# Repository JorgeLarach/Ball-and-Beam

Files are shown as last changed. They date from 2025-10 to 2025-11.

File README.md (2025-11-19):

# Ball and Beam System
Jorge Larach
_11/18/25_

This is my repository for my ball and beam system. Here you will find firmware for an STM32 Nucleo that allows it to interface with a distance sensor and a servo to control the position of a ball along the surface of a beam.

You will also find in the "Notes" directory plots that I used to measure PID performance, written in Python using Matplotlib, part drawings from Fusion, as well as more pictures. 

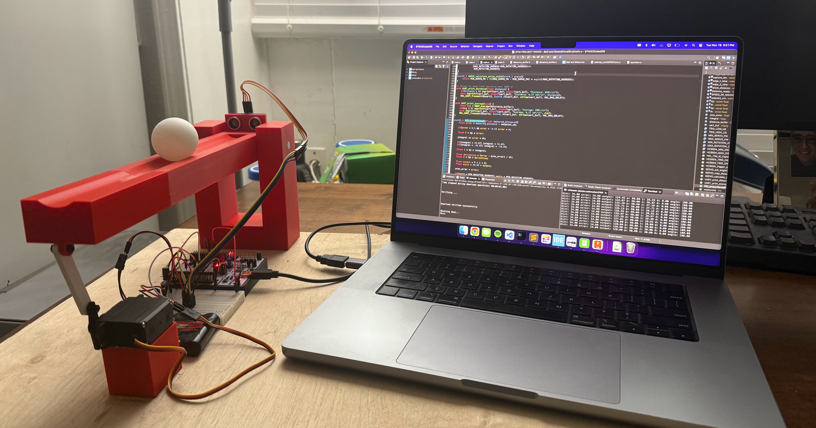
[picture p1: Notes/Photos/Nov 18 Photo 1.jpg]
PID Ball and Beam Project


Below are all of the parts that I used making this project:
* STM32 Nucleo-F401RE
* HC-SR04 Ultrasonic distance sensor
* MG996R Servo
* 6V 2000 mAh NiMH battery
* Small Breadboard
* 3D printed structure (tower, beam, etc.)
* M3 nuts, bolts, and washers
* 1 ping pong ball

Here's a few test results plotted out in Matplotlib. Below is what my first (working) attempt looked like
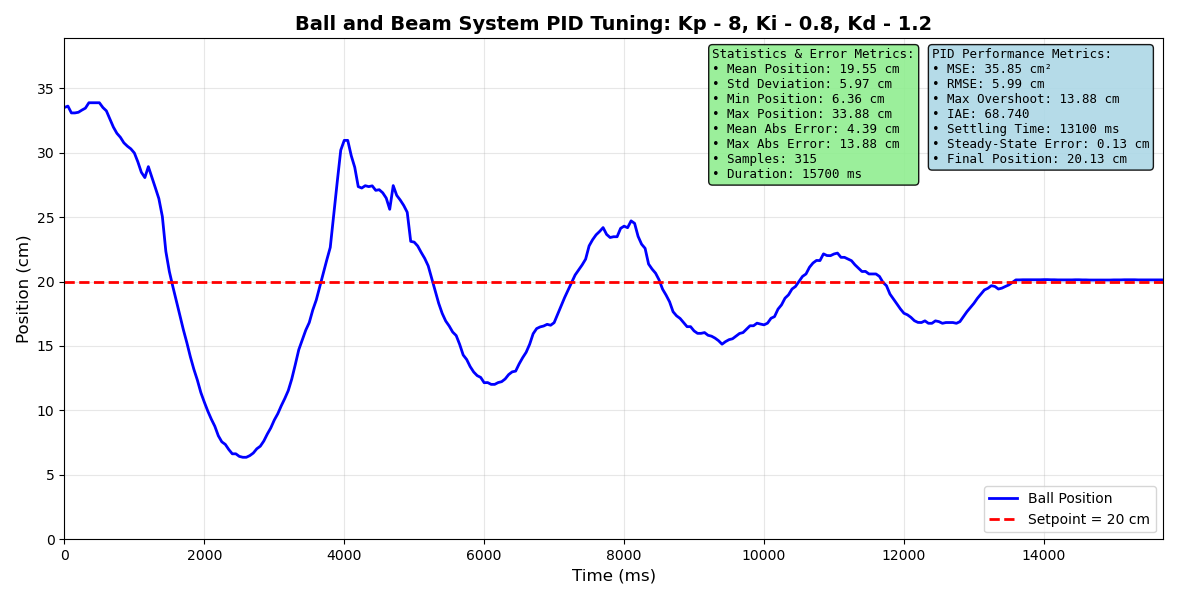
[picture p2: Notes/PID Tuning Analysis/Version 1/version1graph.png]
Version 1


Below is the version currently used by the algorithm. It is definitely far from perfect, but it is a major improvement over the first version (nearly halved the MSE!) There's far less oscillations, but it looks like there's potentially some steady-state error, where the ball approaches the setpoint early on, but seems to hover underneath it for a while.
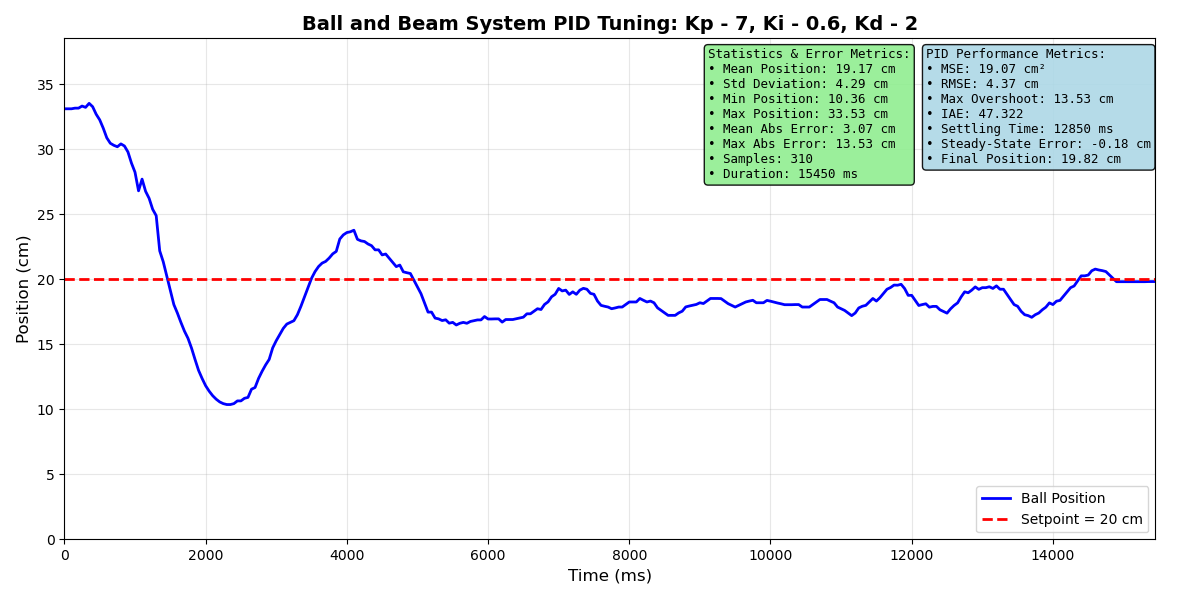
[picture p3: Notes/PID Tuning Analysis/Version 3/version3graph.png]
Version 3


I carved the groove in the beam from a 4 cm diameter circle in Fusion, so it perfectly fits any ping pong ball. My Bambulabs A1 printer couldn't print a beam longer than 25.6 cm due to the print bed size, so I designed it in two steps, consisting of a long bridge part and a short bridge part (during development I decided it would be called a "bridge" instead of "beam"; I don't know exactly what posessed me to do that) using two cylindrical pegs. Below is the Fusion drawing for the long bridge part:
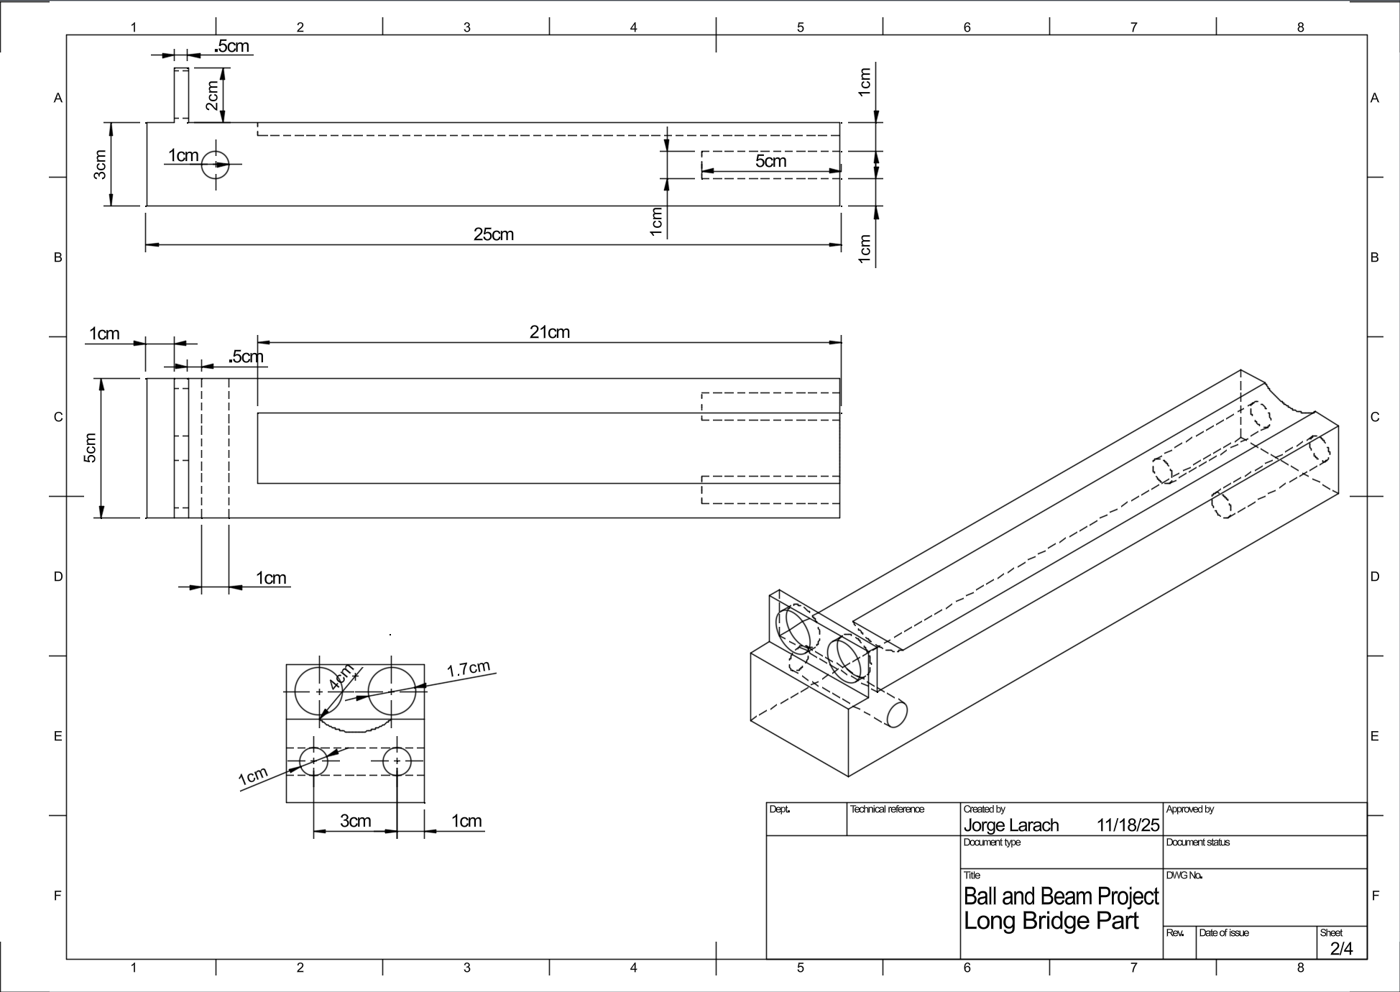
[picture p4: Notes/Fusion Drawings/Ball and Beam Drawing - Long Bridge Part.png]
Fusion drawing for long bridge part


These drawings aren't strictly necessary for anyone interested in replicating my design (all STL files are also included in this repository), but it might give some insight into how all these parts are assembled.
Even though I feel satisfied with the current version, I would like to return to this project someday to address some issues and further improvements, such as:
* The surface of the beam/bridge might be too rough, and it might be causing the ball to slow down or get stuck in places.
* Pretty brutal amounts of sensor noise, despite sample smoothing using a ring buffer.
* The PID performance worsens as the setpoint approaches either edge of the beam; it seems to perform best near the center, at 20 cm.
* The algorithm itself also isn't perfect. I would like to add saturation checking, and keep tuning the gains to obtain better performance.
* I would like to add a second distance sensor next to the tower which sets the setpoint for the algorithm with a cube. That way, I can change the setpoint by moving the cube.
* Circular extender for servo arm. Right now, the bridge only moves +1 cm when servo is at 180 degrees, and -1 cm for 0 degrees. Maybe a larger range of motion improves PID performance?

When I return to this project, it will likely be after my next project, which I'm researching now. I would love to one day build a drone, but I think the most realisting next project I can acheive is a 3 axis robotic arm. Or who knows, maybe I'll find something else that blows my socks off. Overall, though, I'm really happy with where this project is at today. Further work will be detailed in this readme.

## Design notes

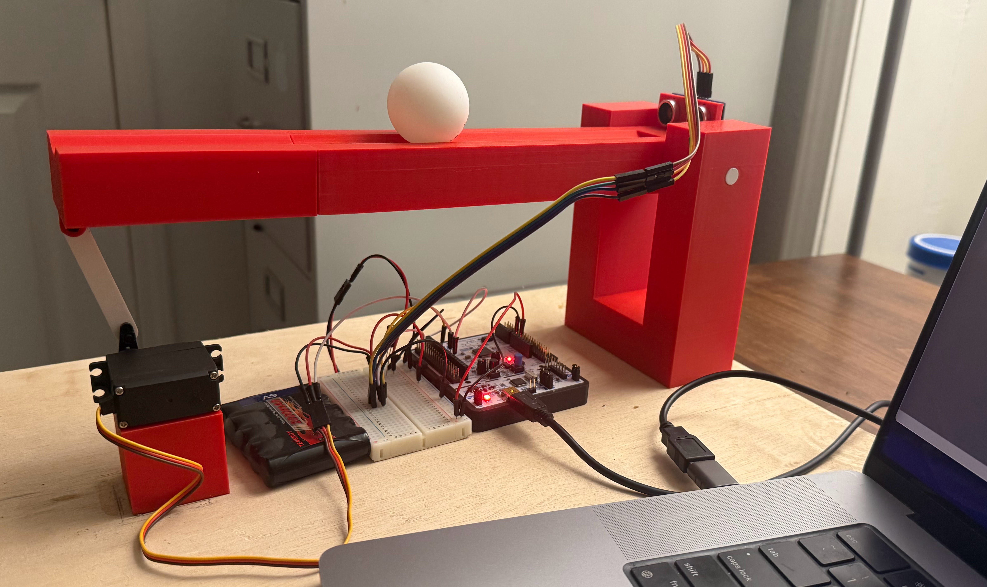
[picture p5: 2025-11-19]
Notes/Photos/Nov 18 Photo 2.jpg

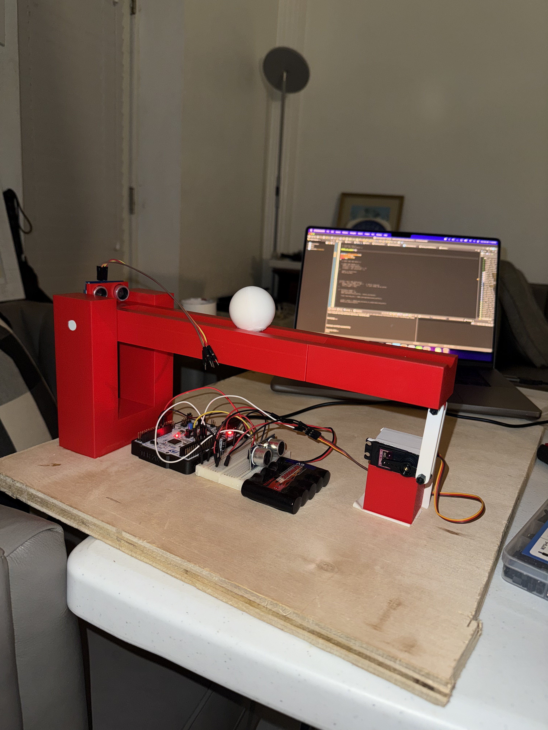
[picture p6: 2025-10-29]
Notes/Photos/Oct 26 Photo 1.jpg

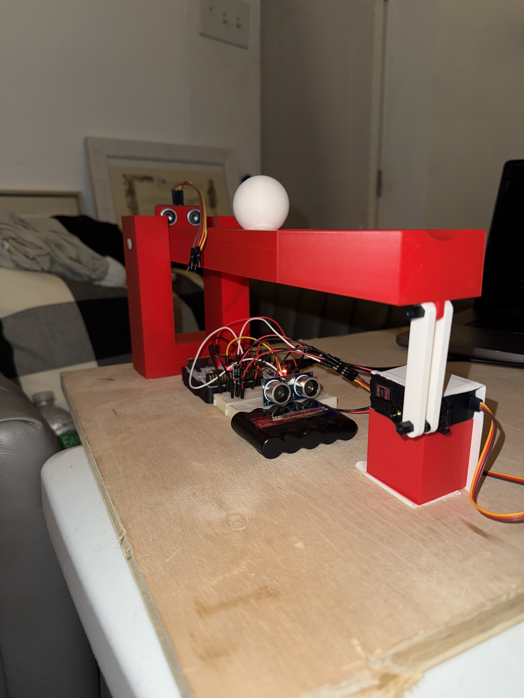
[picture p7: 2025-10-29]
Notes/Photos/Oct 26 Photo 2.jpg

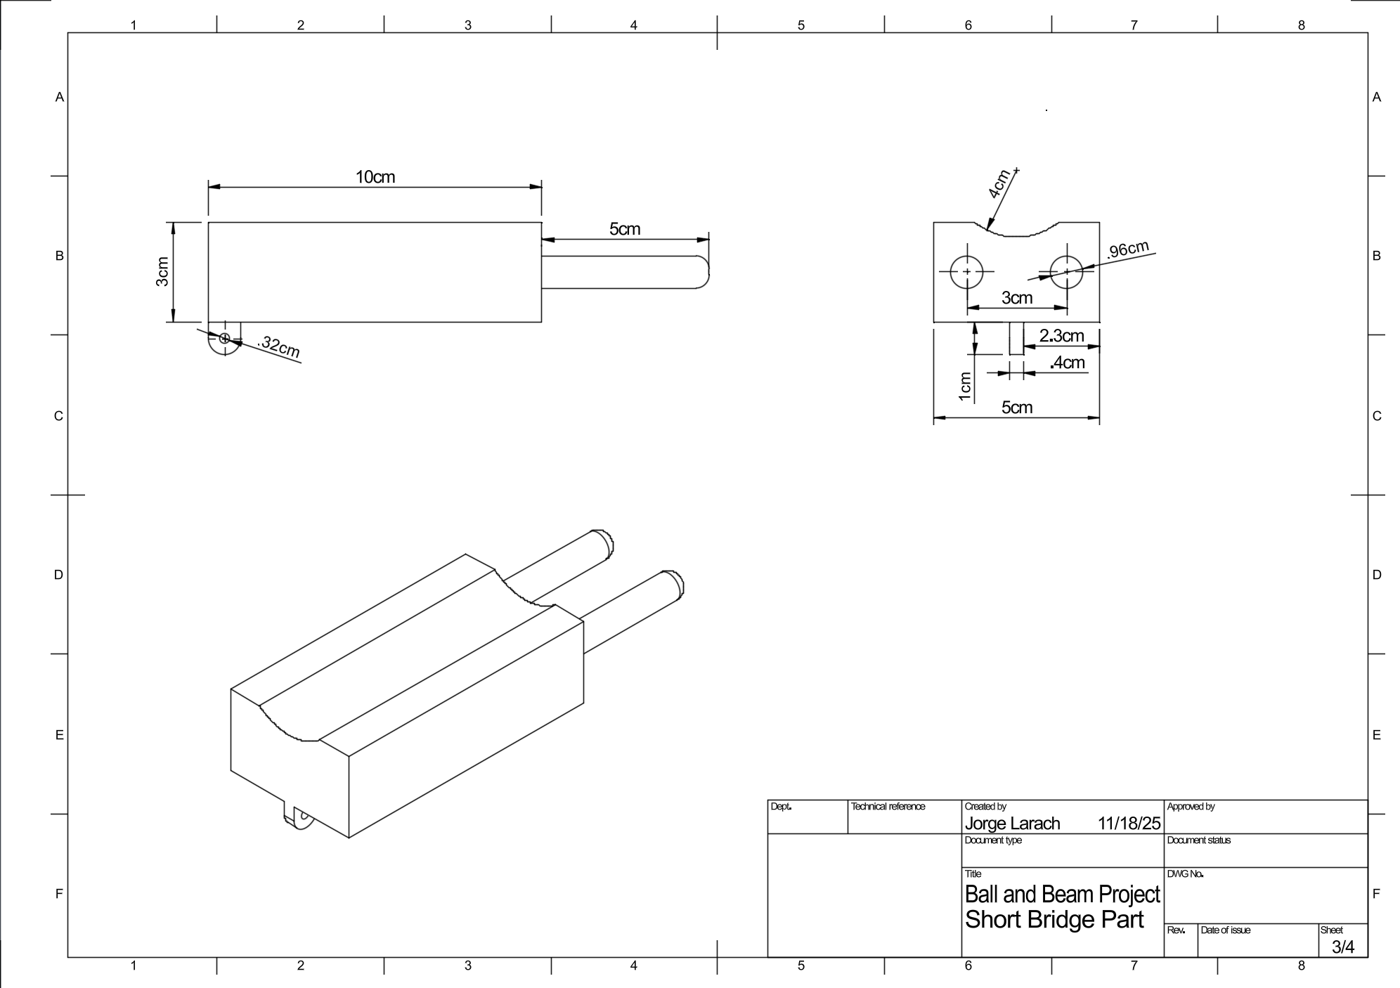
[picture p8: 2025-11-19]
Notes/Fusion Drawings/Ball and Beam Drawing - Short Bridge Part.png

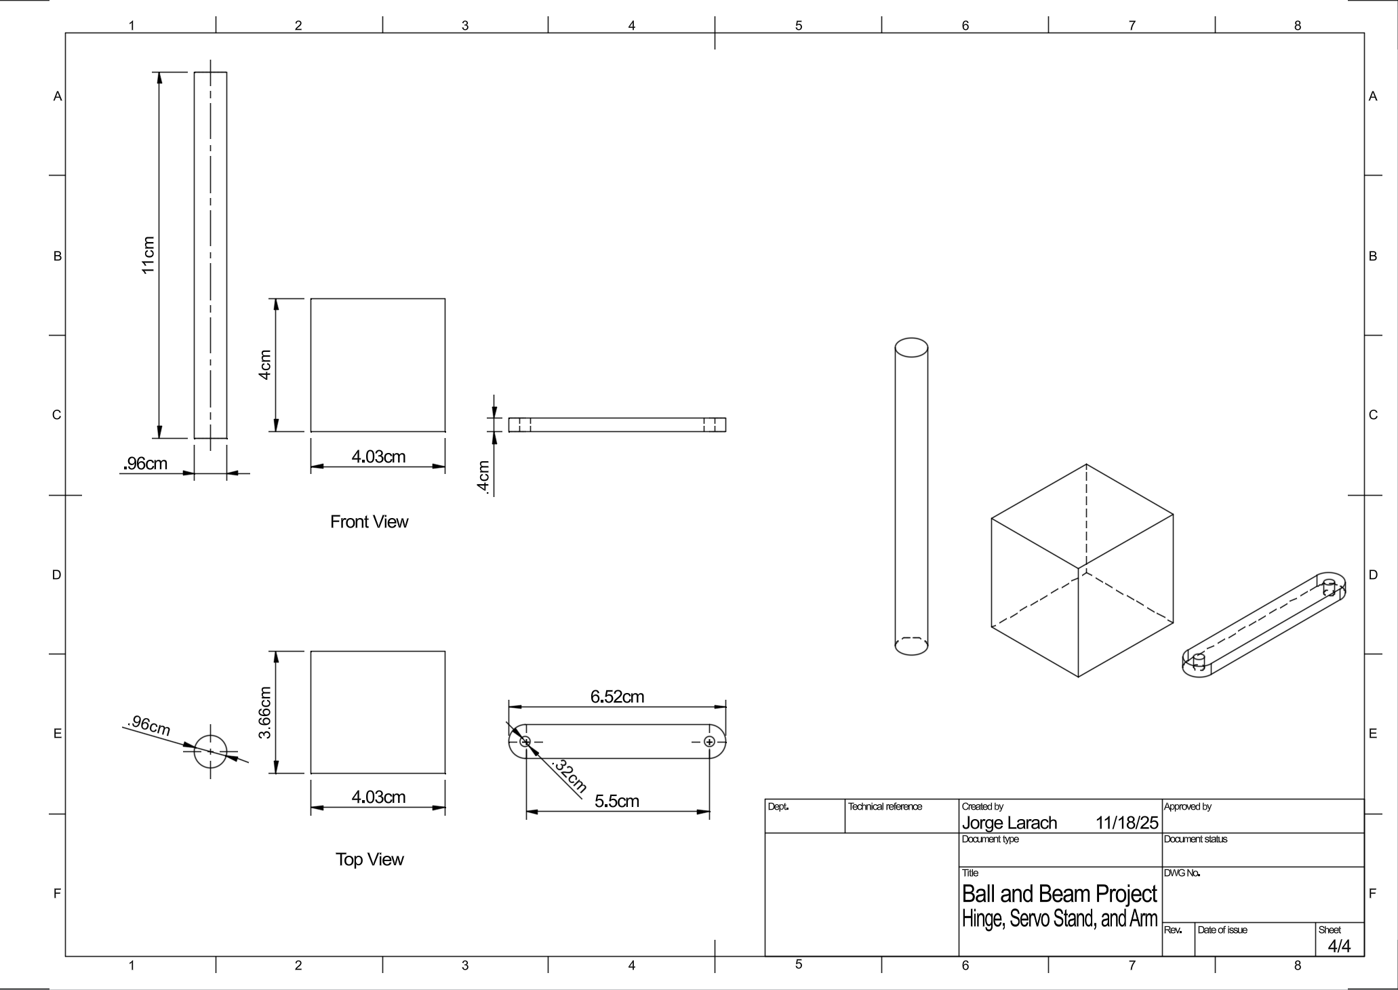
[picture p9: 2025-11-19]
Notes/Fusion Drawings/Ball and Beam Drawing - Hinge, Servo Stand, and Arm.png

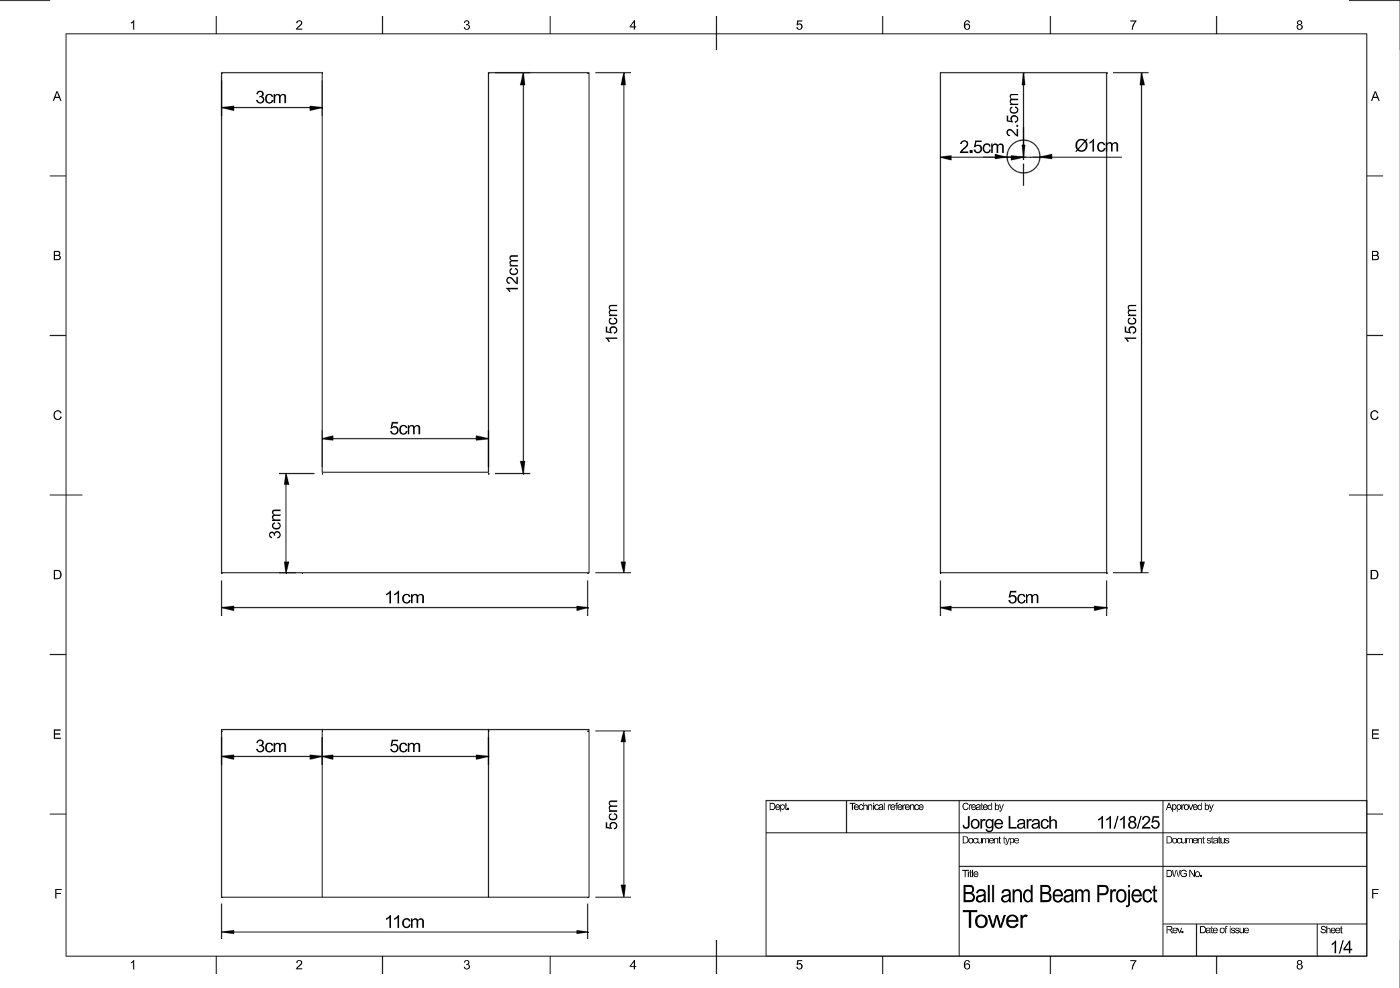
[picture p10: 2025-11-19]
Notes/Fusion Drawings/Ball and Beam Drawing - Tower.png

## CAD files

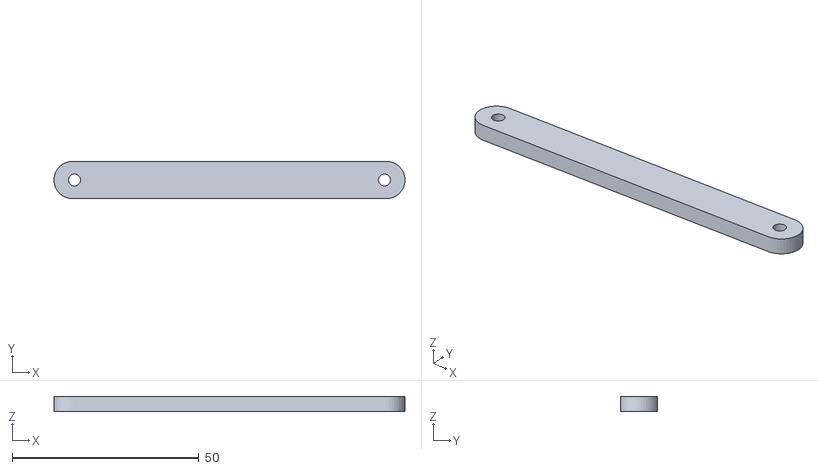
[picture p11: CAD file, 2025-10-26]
3D Prints/Motor Arm V3.stl
94.0 x 10.0 x 4.00

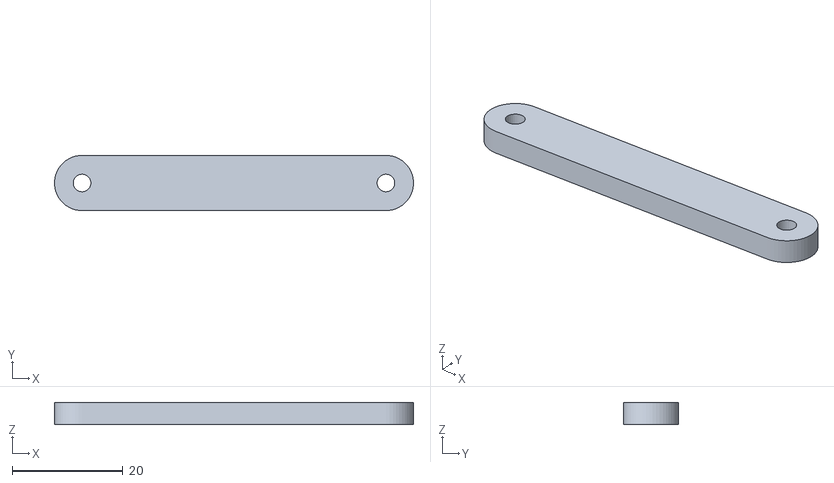
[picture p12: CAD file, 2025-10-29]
Notes/Printing STLs/Motor Arm V4.stl
65.0 x 10.0 x 4.00

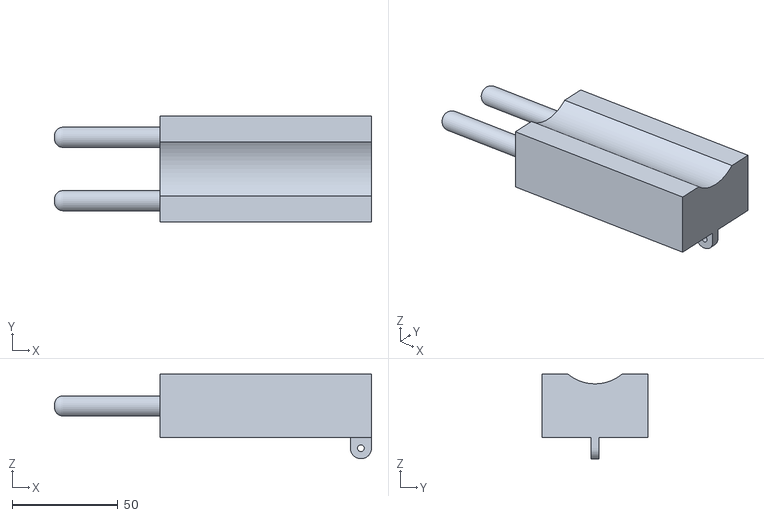
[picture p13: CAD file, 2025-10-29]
Notes/Printing STLs/Bridge Short Part V2.stl
150.0 x 50.0 x 40.0

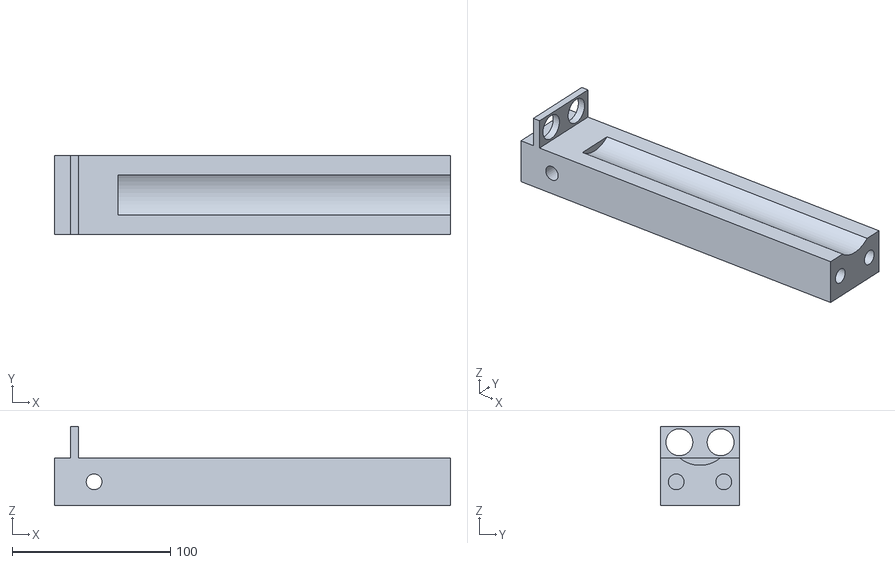
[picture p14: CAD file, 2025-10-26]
Notes/Printing STLs/Bridge Long Part.stl
250.0 x 50.0 x 50.0

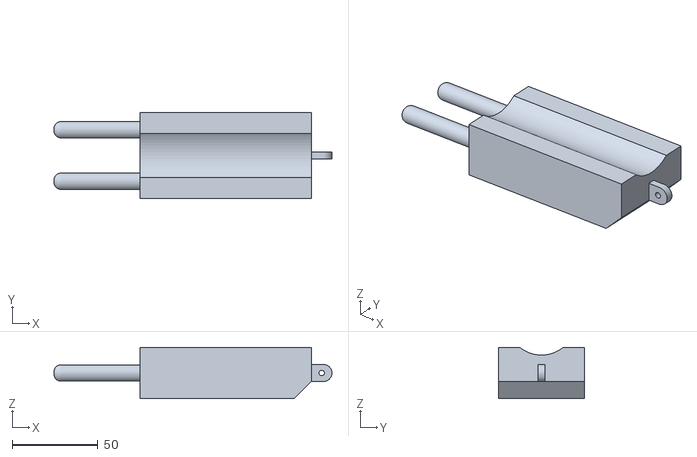
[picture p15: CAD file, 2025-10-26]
3D Prints/Bridge Short Part.stl
162.0 x 50.0 x 30.0

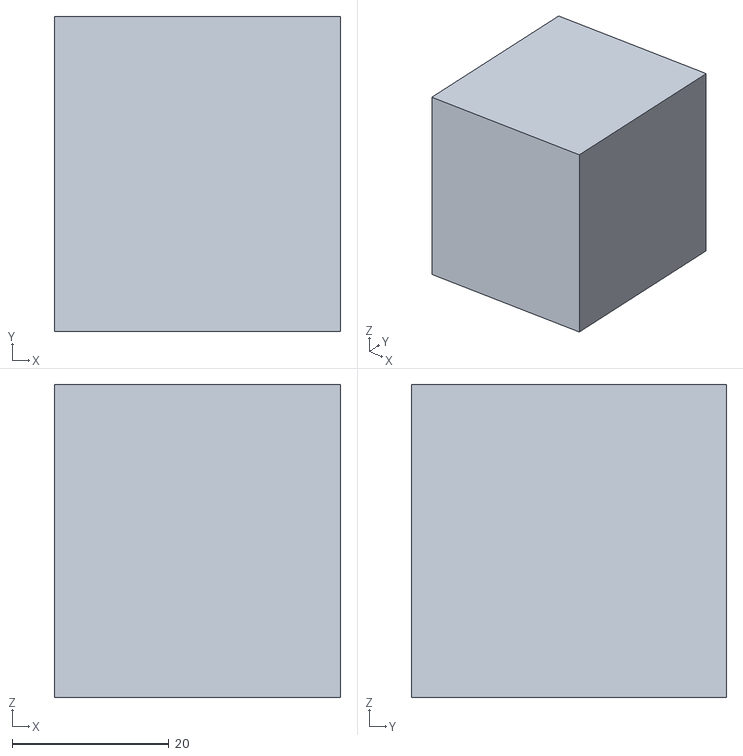
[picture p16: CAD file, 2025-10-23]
Notes/Printing STLs/Motor Stand.stl
36.6 x 40.3 x 40.0

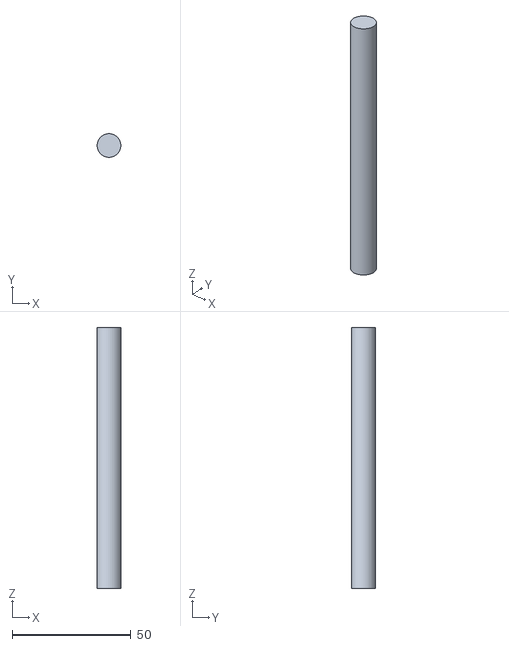
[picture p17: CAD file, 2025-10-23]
3D Prints/Hinge V2.stl
10.0 x 9.97 x 110.0

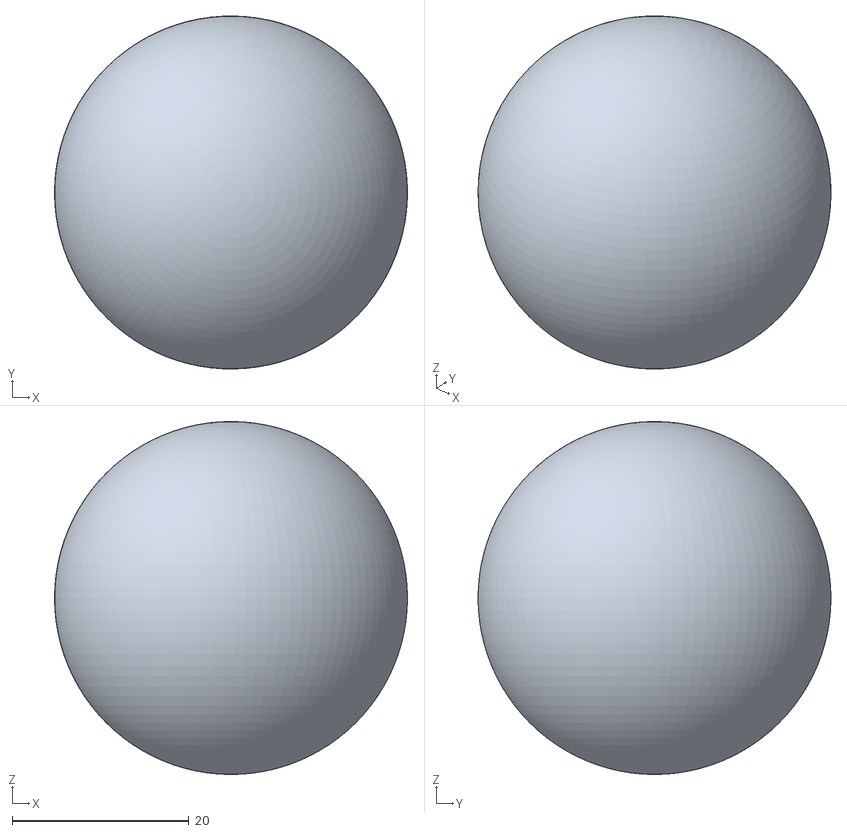
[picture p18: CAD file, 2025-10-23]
Notes/Printing STLs/Ball.stl
40.0 x 40.0 x 40.0

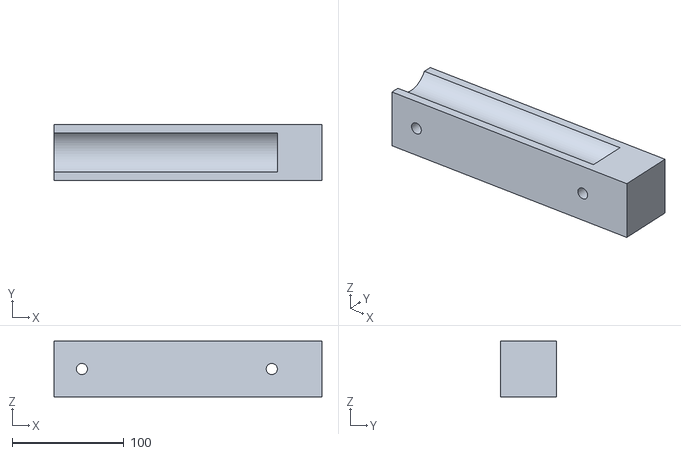
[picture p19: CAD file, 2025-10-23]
3D Prints/Bridge V1.stl
240.0 x 50.0 x 50.0

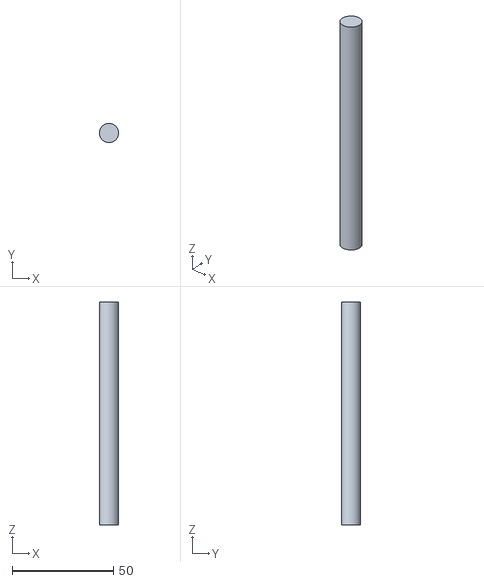
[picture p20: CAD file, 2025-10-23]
Notes/Printing STLs/Hinge V3.stl
9.48 x 9.49 x 110.0

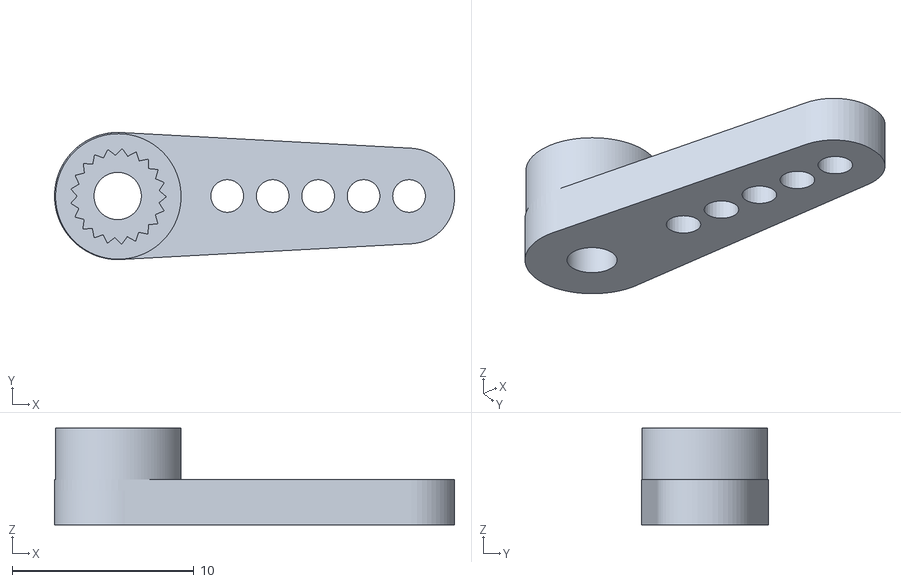
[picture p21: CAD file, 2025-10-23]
3D Prints/ServoMotor Arms MG90S.stl
22.0 x 7.00 x 5.32

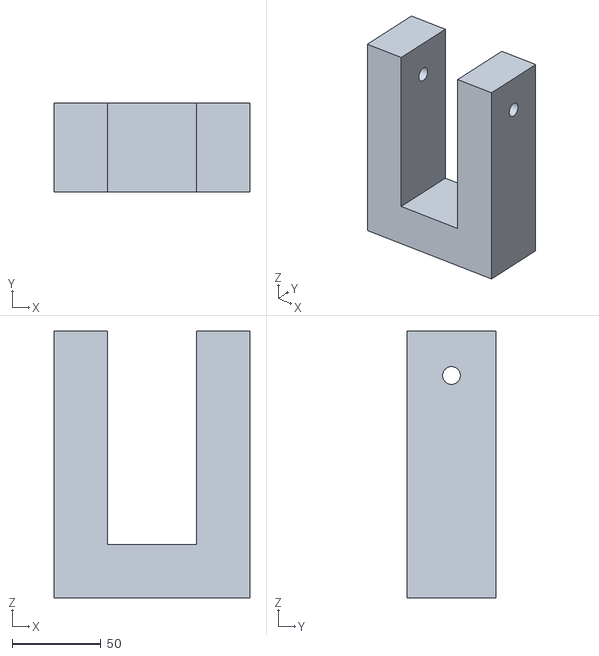
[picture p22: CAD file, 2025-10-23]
Notes/Printing STLs/Tower V3.stl
110.0 x 50.0 x 150.0

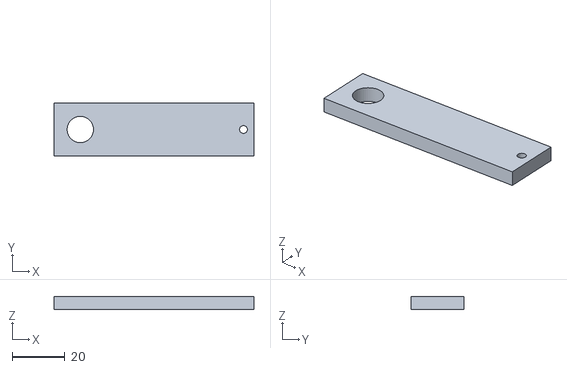
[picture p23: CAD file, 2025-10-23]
3D Prints/Motor Hinge.stl
76.0 x 20.0 x 5.00

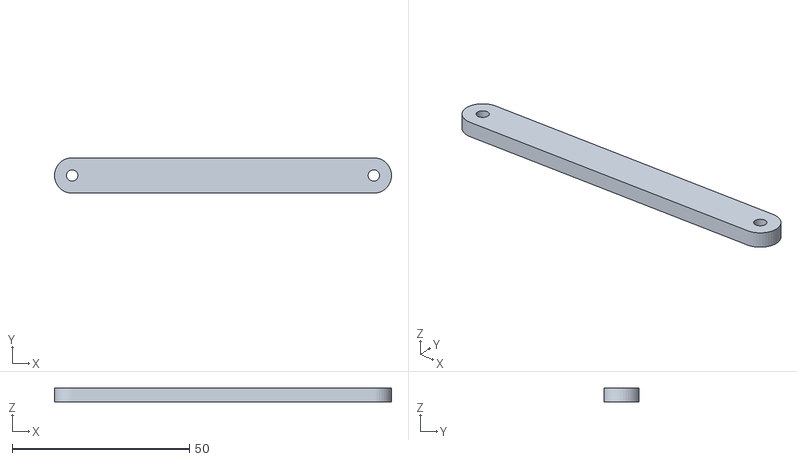
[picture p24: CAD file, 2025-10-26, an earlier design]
3D Prints/Motor Arm V2.stl
95.0 x 10.0 x 4.00

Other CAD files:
3D Prints/Motor Arm.stl
Notes/Printing STLs/Old Models/Motor Arm.stl

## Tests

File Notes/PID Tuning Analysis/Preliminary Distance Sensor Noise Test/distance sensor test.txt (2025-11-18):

30.0
30.0
30.0
30.0
30.0
30.0
30.0
30.0
30.0
30.0
30.0
30.0
30.0
30.0
30.0
30.0
30.0
30.0
30.0
30.0
30.0
30.0
30.0
30.0
30.0
30.0
30.0
30.0
30.0
30.0
29.5
28.8
28.1
28.1
27.0
26.0
24.8
23.4
22.0
20.5
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

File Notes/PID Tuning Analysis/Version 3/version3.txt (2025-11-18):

33.11
33.11
33.11
33.16
33.16
33.32
33.22
33.53
33.27
32.69
32.26
31.62
30.88
30.46
30.30
30.19
30.41
30.25
29.79
28.93
28.23
26.80
27.70
26.76
26.22
25.38
24.89
22.18
21.34
20.25
19.15
18.05
17.40
16.68
16.01
15.46
14.71
13.83
12.99
12.37
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

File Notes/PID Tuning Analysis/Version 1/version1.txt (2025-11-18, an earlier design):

33.51
33.62
33.09
33.09
33.14
33.31
33.46
33.88
33.88
33.88
33.88
33.51
33.25
32.62
31.99
31.51
31.2
30.77
30.51
30.3
29.98
29.29
28.48
28.07
28.92
28.11
27.28
26.44
25.05
22.34
20.78
19.61
18.51
17.39
16.27
15.26
14.17
13.2
12.36
11.39
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

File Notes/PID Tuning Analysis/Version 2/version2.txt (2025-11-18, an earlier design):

32.8
32.28
32.49
32.64
33.06
33.48
34
34
34
34
34
34
34
34
34
34
33.69
33
32.21
31.48
30.53
29.95
29.15
29.1
28.64
28.34
27.05
26.34
24.8
23.62
22.03
21.19
19.9
18.79
17.49
16.63
15.63
14.73
13.77
12.87
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

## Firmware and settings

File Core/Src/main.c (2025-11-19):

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
/* Includes ------------------------------------------------------------------*/
#include "main.h"

/* USER CODE BEGIN Includes */
#include <stdio.h>
#include <stdlib.h>
#include <string.h>
#include <math.h>
#include "distance_buffer.h"

/*
Jorge Larach, September 28 2025
Ball and Beam Project
 */
/* USER CODE END Includes */

TIM_HandleTypeDef htim3;
TIM_HandleTypeDef htim4;

UART_HandleTypeDef huart2;

void SystemClock_Config(void);
static void MX_GPIO_Init(void);
static void MX_USART2_UART_Init(void);
static void MX_TIM3_Init(void);
static void MX_TIM4_Init(void);
/* USER CODE BEGIN PFP */
void HCSR04_TRIG_DWT_init(void);
void HCSR04_TRIG_DWTDelay_us(uint32_t uSec);
void HCSR04_trigger_pulse(void);
uint32_t SERVO_set_angle(uint8_t angle);
uint32_t SERVO_calculate_pulse_width(uint8_t angle);
void UART_print_distance(float distance);
void UART_print_average(void);
uint32_t PID(float measured_distance);
/* USER CODE END PFP */

/* USER CODE BEGIN 0 */

/* HC-SR04 variables and constants */
volatile uint8_t capture_idx = 0;
volatile uint32_t edge_1_time = 0, edge_2_time = 0;
volatile float latest_distance = -1.0f;  // shared between ISR and main
volatile uint8_t distance_ready = 0;     // flag to tell main loop new data is ready
const uint8_t ms_interval = 50; // Interval in ms between sensor readings (never < 50)
const float SPEED_OF_SOUND_CM_US = 0.0343f; // cm per microsecond

/* PID controller variables and constants */
const float Kp = 7.0f;
const float Ki = 0.6f;
const float Kd = 2.0f;
const uint8_t setpoint_cm = 20;
const float dt = (float)ms_interval / 1000.0;   // 50ms update rate = 20Hzs
float prev_error = 0.0f;
float integral = 0.0f;

DBUF distance_buffer;

char uart_buf[100] = {'\0'};

#define TRIG_LOW_US          3
#define TRIG_HIGH_US         10
#define MIN_SERVO_PW         250  // 0.5ms duty cycle, 0 degrees
#define MAX_SERVO_PW         1250 // 2.5s  duty cycle, 180 degrees
#define MIN_ROTATION_DEGREES 0
#define MAX_ROTATION_DEGREES 180  // Max angle a servo can rotate
#define HCSR04_MIN_DIST_CM   3
#define HCSR04_MAX_DIST_CM   34

void HAL_TIM_IC_CaptureCallback(TIM_HandleTypeDef *htim)
{
    if(capture_idx == 0){
        edge_1_time = HAL_TIM_ReadCapturedValue(htim, TIM_CHANNEL_1);
        capture_idx = 1;
    } else {
        edge_2_time = HAL_TIM_ReadCapturedValue(htim, TIM_CHANNEL_1);
        capture_idx = 0;
        uint32_t edge_diff = (edge_2_time >= edge_1_time) ?
                             (edge_2_time - edge_1_time) :
                             ((htim3.Init.Period - edge_1_time) + edge_2_time);

        float distance_cm = ((float)edge_diff) * (SPEED_OF_SOUND_CM_US / 2.0f);
        if(distance_cm > HCSR04_MAX_DIST_CM) distance_cm = HCSR04_MAX_DIST_CM;
        if(distance_cm < HCSR04_MIN_DIST_CM) distance_cm = HCSR04_MIN_DIST_CM;
        latest_distance = distance_cm;

        distance_ready = 1;
    }
}

/* Initialize DWT for microsecond delays */
void HCSR04_TRIG_DWT_init(void){
    CoreDebug->DEMCR |= CoreDebug_DEMCR_TRCENA_Msk;
    DWT->CYCCNT = 0;
    DWT->CTRL |= DWT_CTRL_CYCCNTENA_Msk;
}

/* Microsecond delay using DWT */
void HCSR04_TRIG_DWTDelay_us(uint32_t us) {
    uint32_t cycles = us * (SystemCoreClock / 1000000UL);
    uint32_t start = DWT->CYCCNT;
    while ((DWT->CYCCNT - start) < cycles);
}

void HCSR04_trigger_pulse(void){
    // Trigger pulse
    HAL_GPIO_WritePin(TRIG_GPIO_Port, TRIG_Pin, GPIO_PIN_RESET);
    HCSR04_TRIG_DWTDelay_us(TRIG_LOW_US);
    HAL_GPIO_WritePin(TRIG_GPIO_Port, TRIG_Pin, GPIO_PIN_SET);
    HCSR04_TRIG_DWTDelay_us(TRIG_HIGH_US);
    HAL_GPIO_WritePin(TRIG_GPIO_Port, TRIG_Pin, GPIO_PIN_RESET);
}

uint32_t SERVO_set_angle(uint8_t angle){
	uint32_t pulse_width = SERVO_calculate_pulse_width(angle);
	htim4.Instance->CCR1 = pulse_width;
	return pulse_width;
}

// Prototyping function
uint8_t SERVO_map_distance_to_angle(float prec){
	return (uint8_t)((prec-HCSR04_MIN_DIST_CM)/
		    (HCSR04_MAX_DIST_CM - HCSR04_MIN_DIST_CM)*
			(MAX_ROTATION_DEGREES-MIN_ROTATION_DEGREES))+
			 MIN_ROTATION_DEGREES;
}

uint32_t SERVO_calculate_pulse_width(uint8_t angle){
	return MIN_SERVO_PW + (((MAX_SERVO_PW - MIN_SERVO_PW) * angle)/MAX_ROTATION_DEGREES);
}

/* Helper to send float distance over UART */
void UART_print_distance(float distance) {
    if(distance < 0) snprintf(uart_buf, sizeof(uart_buf), "Distance: ERR\r\n");
    else snprintf(uart_buf, sizeof(uart_buf), "Distance: %.1f cm\r\n", distance);
    HAL_UART_Transmit(&huart2, (uint8_t*)uart_buf, strlen(uart_buf), HAL_MAX_DELAY);
}

void UART_print_average(void) {
	float avg = DBUF_average(&distance_buffer);
    if(avg < 0) snprintf(uart_buf, sizeof(uart_buf), "Average: ERR\r\n");
    else snprintf(uart_buf, sizeof(uart_buf), "Average: %.1f cm\r\n", avg);
    HAL_UART_Transmit(&huart2, (uint8_t*)uart_buf, strlen(uart_buf), HAL_MAX_DELAY);
}

uint32_t PID(float measured_distance){
	float error = measured_distance - setpoint_cm;

	if(error < 0.5 && error > -0.5) error = 0;

    float P = Kp * error;

    integral += error * dt;

    if(integral > 50.0f) integral = 50.0f;
    if(integral < -50.0f) integral = -50.0f;

    float I = Ki * integral;

    float derivative = (error - prev_error) / dt;
    float D = Kd * derivative;

    float output = P + I + D;
    float angle = 90.0f + output;

    prev_error = error;

    if(angle < MIN_ROTATION_DEGREES) angle = MIN_ROTATION_DEGREES;
    if(angle > MAX_ROTATION_DEGREES) angle = MAX_ROTATION_DEGREES;

//    snprintf(uart_buf, sizeof(uart_buf), "%.2f\r\n", measured_distance);
    snprintf(uart_buf, sizeof(uart_buf), "dist: %.2f error: %.2f output: %.2f p: %.2f i: %.2f d: %.2f angle: %.2f \r\n", measured_distance, error, output, P, I, D, angle);
//    snprintf(uart_buf, sizeof(uart_buf), "dist: %.2f error: %.2f output: %.2f angle: %.2f \r\n", measured_distance, error, output, angle);
//    snprintf(uart_buf, sizeof(uart_buf), "error: %.5f output: %.5f angle: %.5f \r\n", error, output, angle);

    HAL_UART_Transmit(&huart2, (uint8_t*)uart_buf, strlen(uart_buf), HAL_MAX_DELAY);
    return (uint32_t)angle;
}

/* USER CODE END 0 */

/**
  * @brief  The application entry point.
  * @retval int
  */
int main(void)
{

  /* MCU Configuration--------------------------------------------------------*/

  /* Reset of all peripherals, Initializes the Flash interface and the Systick. */
  HAL_Init();

  /* Configure the system clock */
  SystemClock_Config();

  /* Initialize all configured peripherals */
  MX_GPIO_Init();
  MX_USART2_UART_Init();
  MX_TIM3_Init();
  MX_TIM4_Init();
  /* USER CODE BEGIN 2 */
  HAL_TIM_IC_Start_IT(&htim3, TIM_CHANNEL_1); // Input capture on ECHO
  HAL_TIM_PWM_Start(&htim4, TIM_CHANNEL_1);   // PWM for servo
  HCSR04_TRIG_DWT_init();                     // us delay for TRIG pulse
  DBUF_init(&distance_buffer);                // Ring buffer for distance readings

  /* USER CODE END 2 */

  /* Infinite loop */
  /* USER CODE BEGIN WHILE */

  SERVO_set_angle(90);

  uint32_t last_trigger = 0;
  while (1)
  {
    /* USER CODE END WHILE */

    /* USER CODE BEGIN 3 */

	uint32_t now = HAL_GetTick();
	if (now - last_trigger >= ms_interval) {   // 50 ms interval
	    HCSR04_trigger_pulse();       // just sends 10 µs pulse
	    last_trigger = now;
	}

	if (distance_ready) {
	    distance_ready = 0;
	    DBUF_add(&distance_buffer, latest_distance);
	    float current = DBUF_average(&distance_buffer);
	    uint32_t action = PID(current);
	    SERVO_set_angle(action);
	}
  }
  /* USER CODE END 3 */
}

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


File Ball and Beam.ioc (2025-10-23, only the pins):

Mcu.UserName=STM32F401RETx
PA2.Signal=USART2_TX
PA3.Signal=USART2_RX
PA5.GPIO_Label=LED
PA5.Signal=GPIO_Output
PA6.Signal=S_TIM3_CH1
PA8.GPIO_Label=TRIG
PA8.Signal=GPIO_Output
PB6.Signal=S_TIM4_CH1
PC13-ANTI_TAMP.GPIO_Label=Button
PC13-ANTI_TAMP.Signal=GPIO_Input

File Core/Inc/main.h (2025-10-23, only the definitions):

#define Button_Pin GPIO_PIN_13
#define Button_GPIO_Port GPIOC
#define LED_Pin GPIO_PIN_5
#define LED_GPIO_Port GPIOA
#define TRIG_Pin GPIO_PIN_8
#define TRIG_GPIO_Port GPIOA

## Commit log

2025-10-23 Pushing existing project code
    [Ball.stl, Bridge V1.stl, Hinge V2.stl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]
2025-10-26 Redesigned every part, added STLs to project.
    [Bridge Long Part.stl, Bridge Short Part.stl, Motor Arm V2.stl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]
2025-10-26 organized old stls into a folder, made new motor arm stl
    [Bridge V1.stl, Hinge V2.stl, Motor Arm V2.stl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]
2025-10-29 reimplemented sensor control, redesigned some parts
    [Bridge Short Part V2.stl, Bridge Short Part.stl, Motor Arm V3.stl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]
2025-10-31 working version pre-PID
2025-11-11 early version of PID controller. been working on tuning parameters
2025-11-18 reorganized folder structure, wrote python script with matplotlib to visualize and analyze pid performance. further development will come down the road
2025-11-19 included fusion drawings, did some more reorganizing
    [Ball.stl, Bridge Long Part.stl, Bridge Short Part V2.stl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]

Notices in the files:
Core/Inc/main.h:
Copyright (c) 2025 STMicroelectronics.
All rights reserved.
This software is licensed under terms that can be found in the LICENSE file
